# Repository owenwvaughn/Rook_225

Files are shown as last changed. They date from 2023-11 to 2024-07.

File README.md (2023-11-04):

This is a 225x225 build volume printer based on the rook 180 by Rolohaun, 
that uses the BambuLabs P1P hotend in place of the stock hotend.
It's a modification of the work done by woodknight and Kanrog for the rook 180 turned.

It uses an Ender 3 Bed

 [https://github.com/WoodKnight58/Rook-180-Turned](url)

[https://www.printables.com/model/365707-rook-235-225-mod](url)


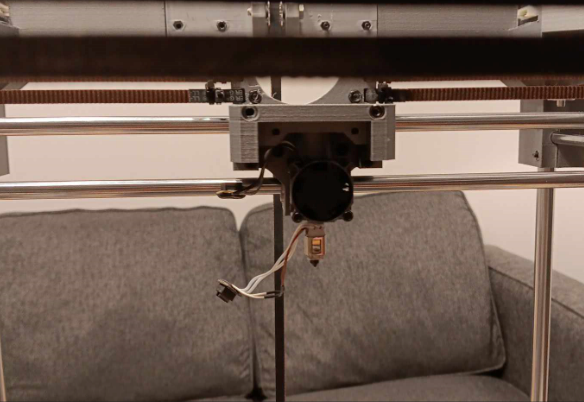
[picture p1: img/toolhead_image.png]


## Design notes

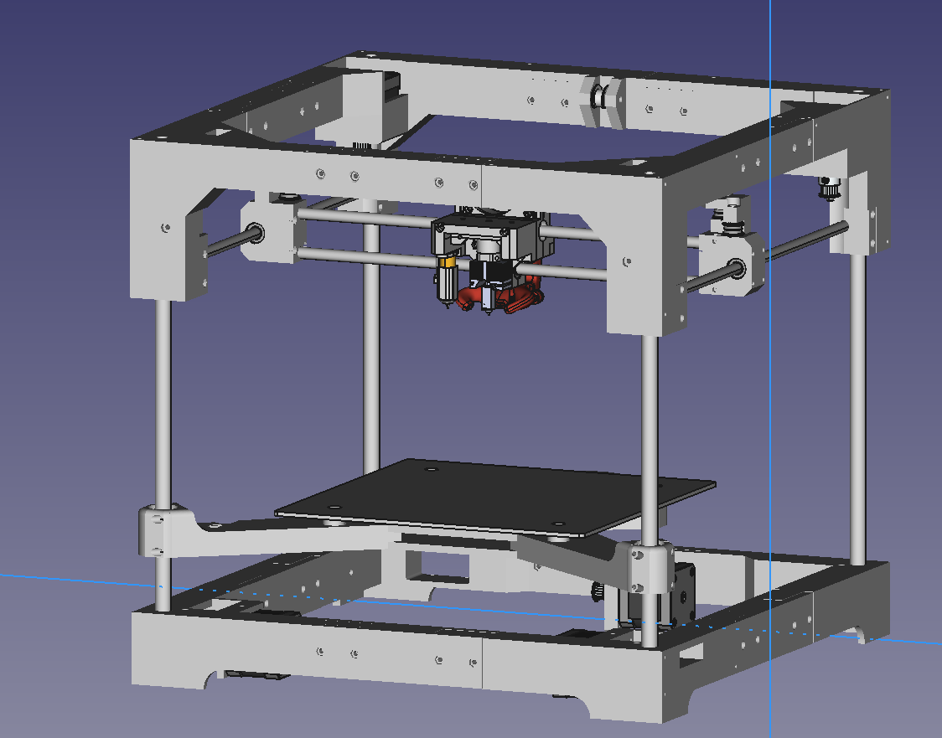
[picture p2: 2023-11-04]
img/frame_image.png

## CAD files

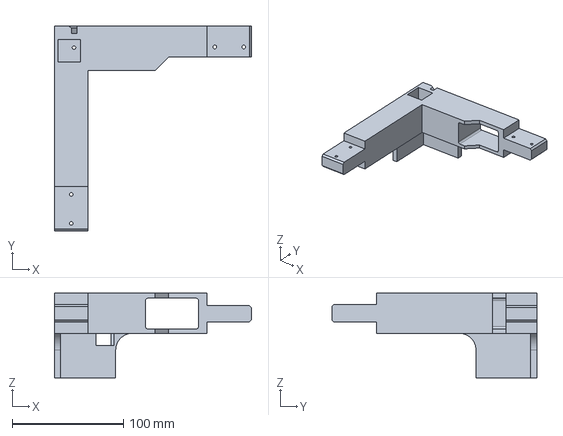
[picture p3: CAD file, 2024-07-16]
printer/cad/FDM/Rear_left_Bottom_Frame.FCStd
177.0 x 184.5 x 76.0 mm

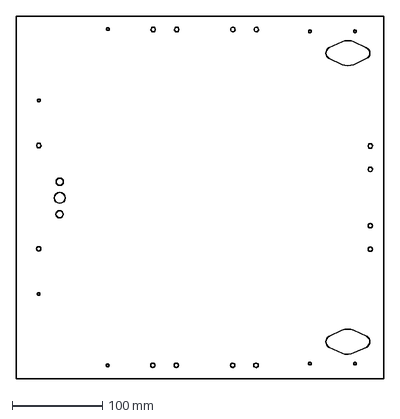
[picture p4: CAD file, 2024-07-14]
printer/cad/MISC/top_panel.dxf
407.3 x 401.7 mm

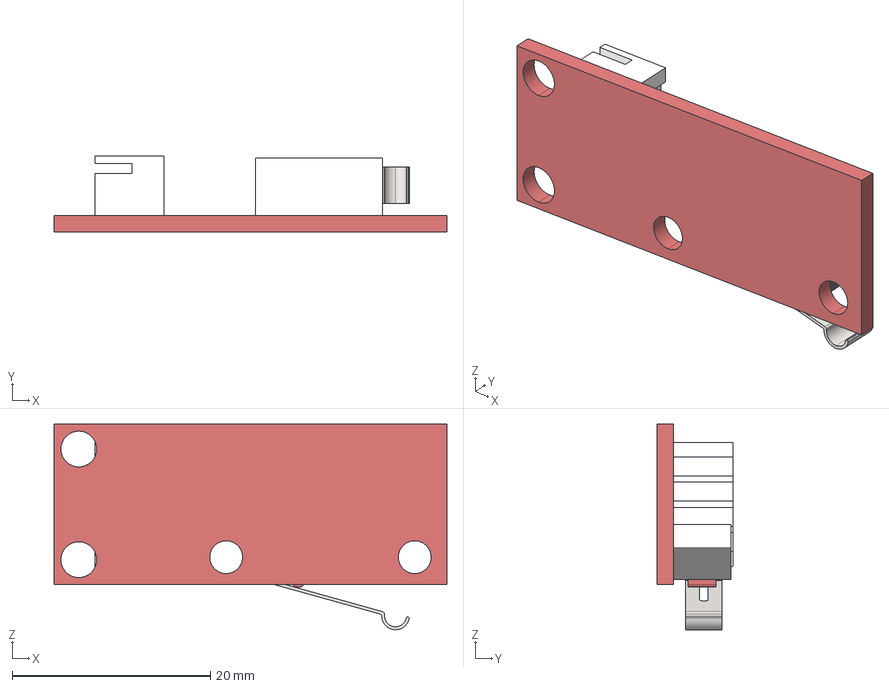
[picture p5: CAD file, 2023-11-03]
printer/cad/PCB/limit-switch.STEP
39.6 x 7.63 x 20.7 mm

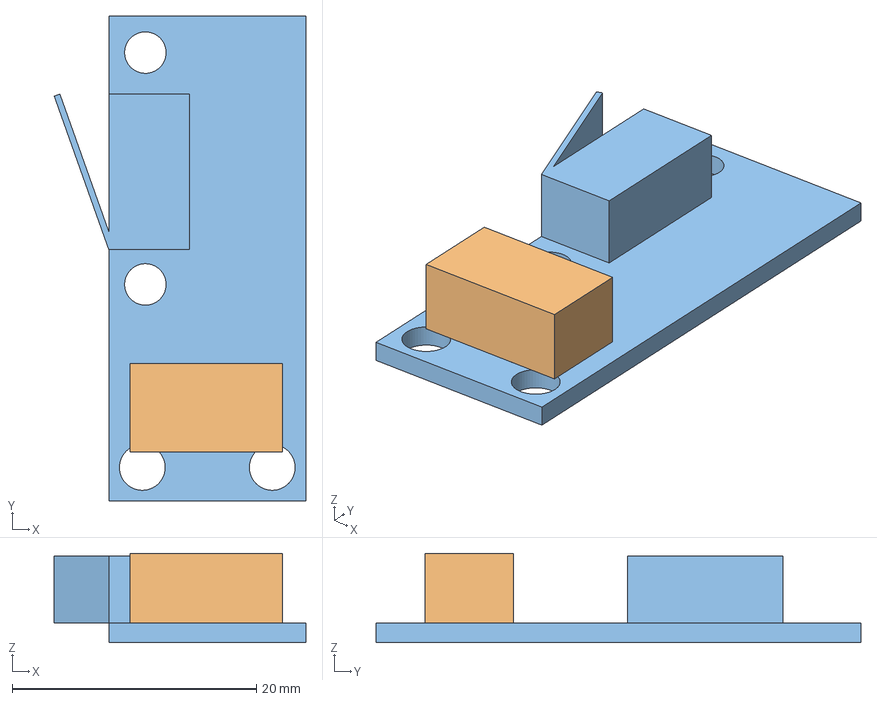
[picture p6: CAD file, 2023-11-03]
printer/pcb/limit-switch/limit-switch.FCStd
20.6 x 39.8 x 7.30 mm

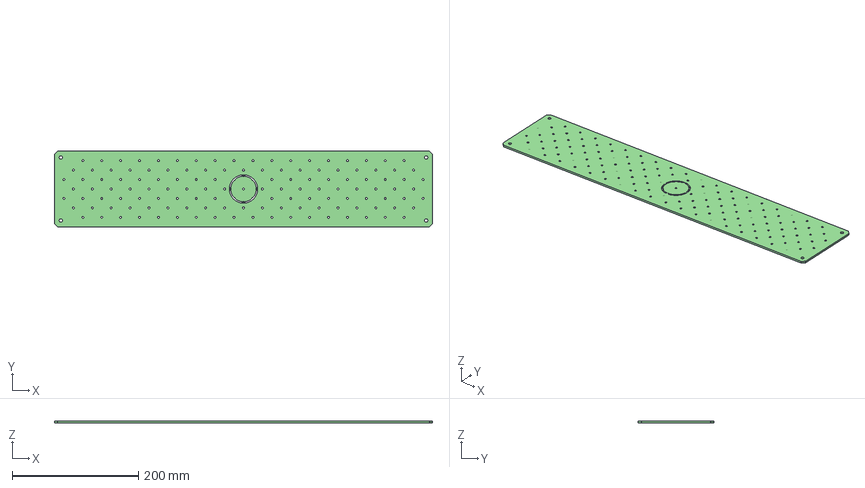
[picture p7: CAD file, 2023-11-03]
printer/pcb/staging-plate/staging-plate.STEP
600.0 x 120.0 x 3.00 mm

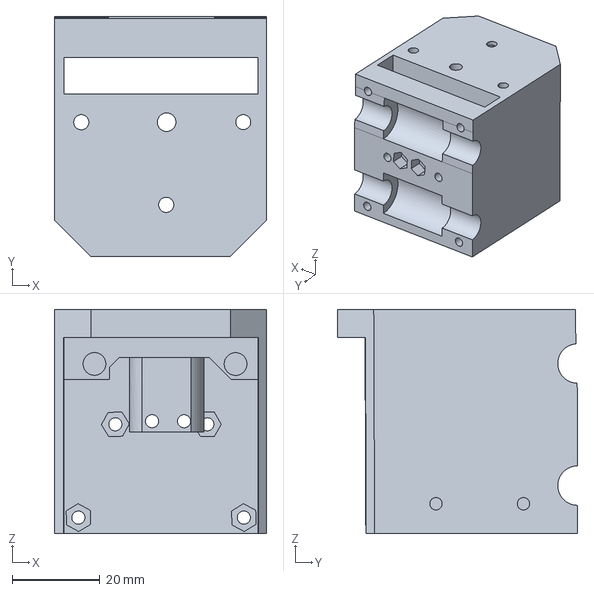
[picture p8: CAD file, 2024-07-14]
printer/cad/FDM/Compact_X_Carriage_Front.FCStd
48.5 x 54.8 x 51.2 mm

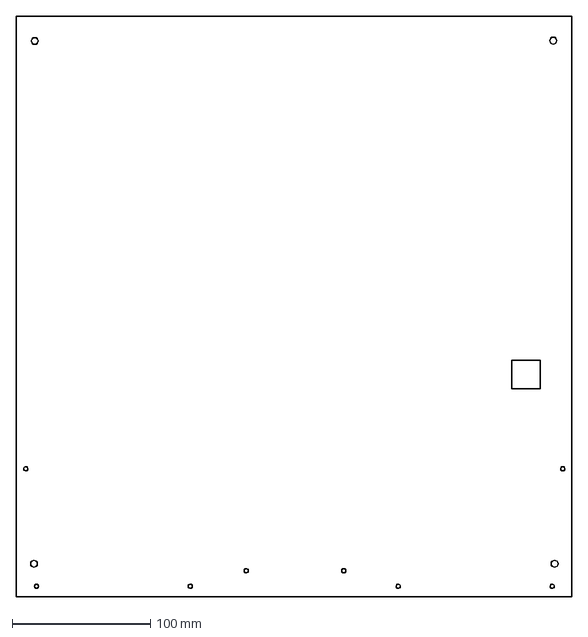
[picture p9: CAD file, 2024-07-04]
printer/cad/MISC/rear_panel.dxf
401.9 x 420.0 mm

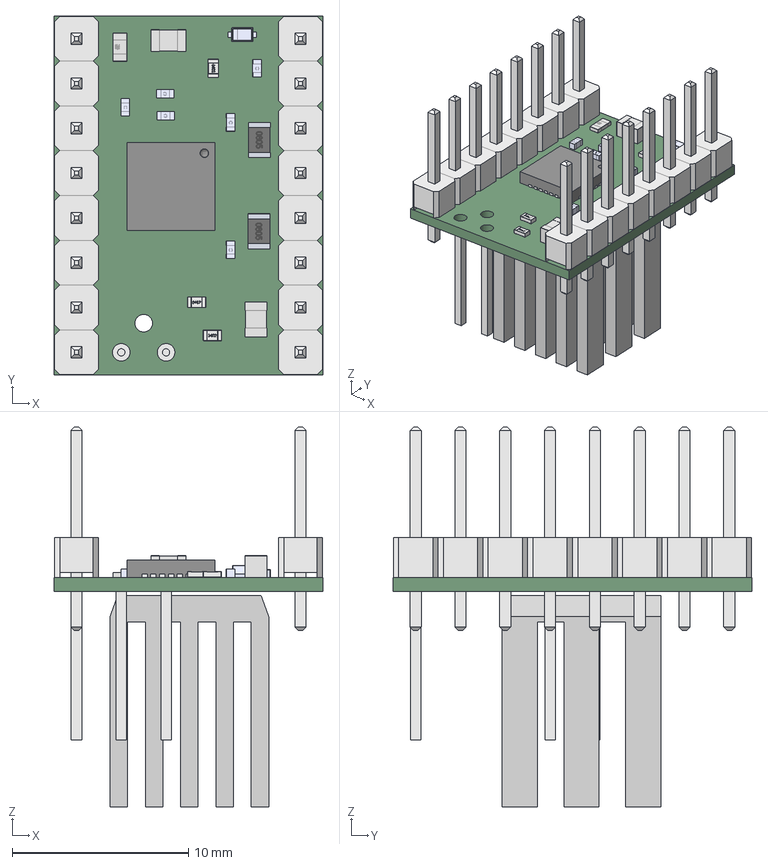
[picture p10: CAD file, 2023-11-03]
printer/cad/PCB/TMC2209-V3_0.FCStd
15.2 x 20.3 x 21.5 mm

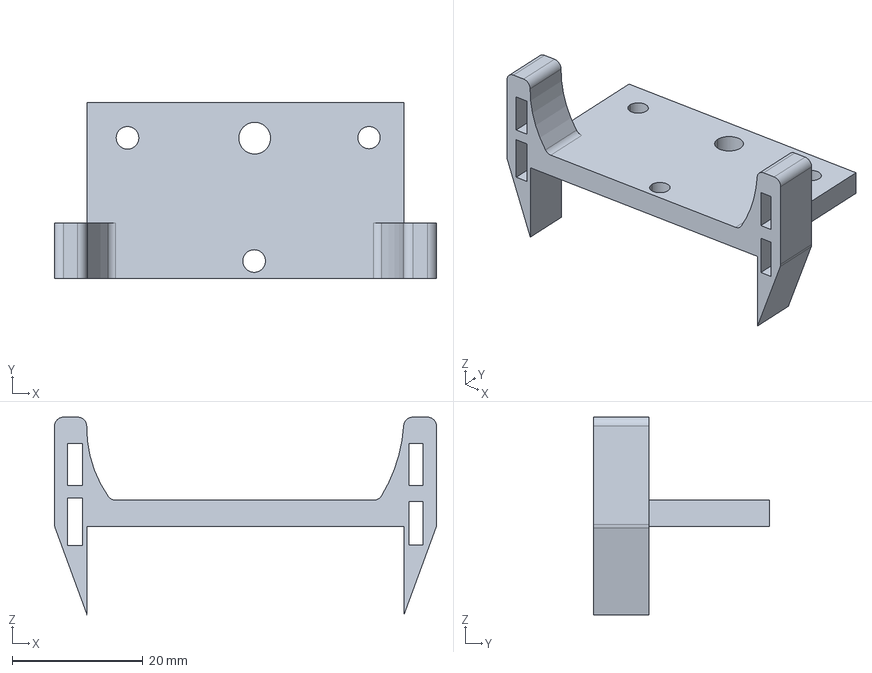
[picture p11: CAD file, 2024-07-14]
printer/cad/FDM/hotend_ears.FCStd
58.5 x 27.0 x 30.3 mm

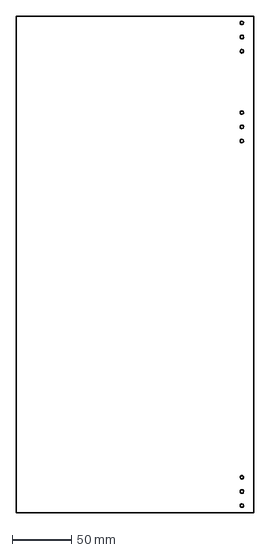
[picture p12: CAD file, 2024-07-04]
printer/cad/MISC/front_panel_left.dxf
200.7 x 419.9 mm

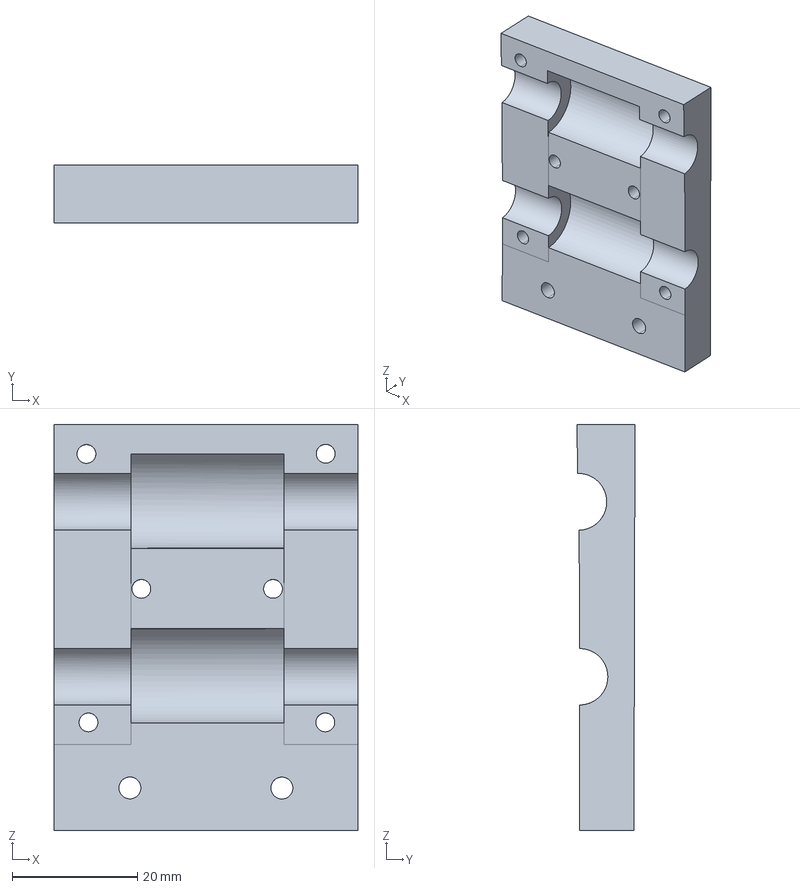
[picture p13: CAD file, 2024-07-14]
printer/cad/FDM/Compact_X_Carriage_Rear.FCStd
48.5 x 9.26 x 64.8 mm

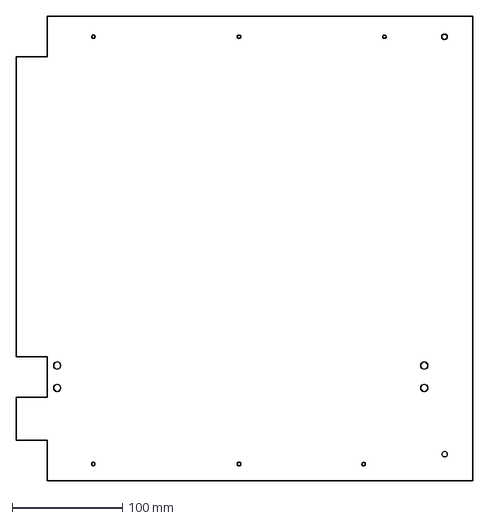
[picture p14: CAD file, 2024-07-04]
printer/cad/MISC/side_panel.dxf
413.8 x 420.4 mm

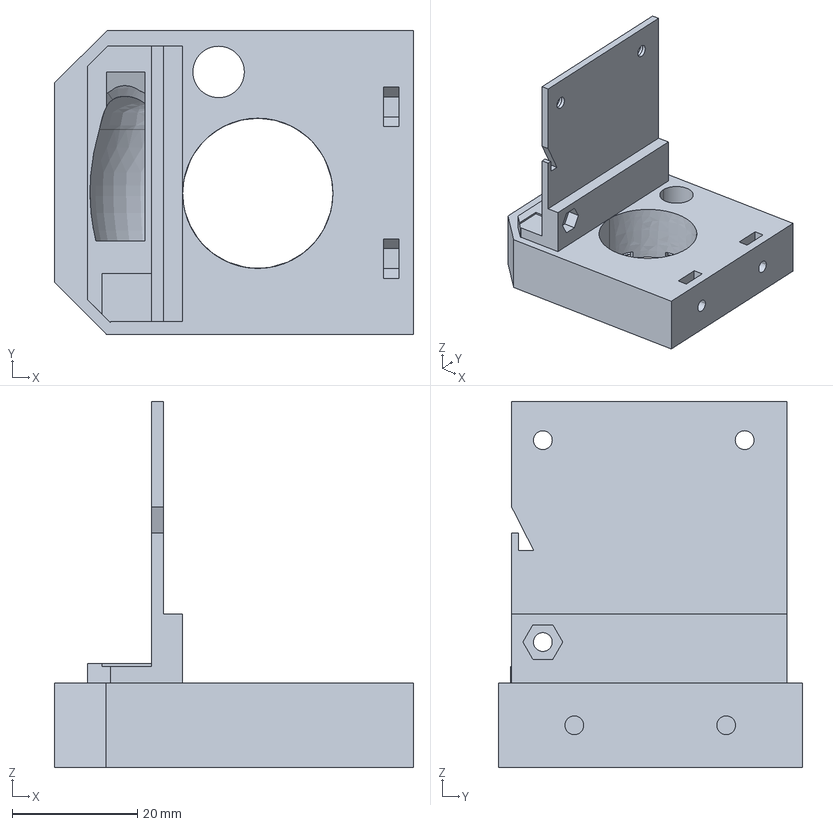
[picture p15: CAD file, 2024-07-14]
printer/cad/FDM/toolhead_toroid.FCStd
57.4 x 48.5 x 58.5 mm

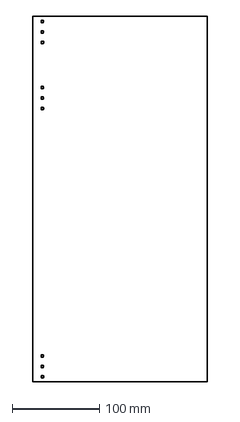
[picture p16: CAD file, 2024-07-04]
printer/cad/MISC/front_panel_right.dxf
200.7 x 419.9 mm

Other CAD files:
printer/cad/FDM/Compact_X_Carriage_Plate.FCStd
printer/cad/FDM/Compact_X_Carriage_Plate-BodyBaseFeature.step
printer/cad/FDM/Bottom_front_right_frame.FCStd
printer/cad/FDM/TOP_Right_Front_Frame.FCStd
printer/cad/FDM/Bed_Standoff.FCStd
printer/cad/FDM/Bed_mount_Center.FCStd
printer/cad/FDM/Bottom_frame_connector.FCStd
printer/cad/FDM/Bottom_front_left_frame.FCStd
printer/cad/FDM/Bottom_front_right_frame_logo.FCStd
printer/cad/FDM/Extrusion_corner.FCStd
printer/cad/FDM/Front_Y_Clamps.FCStd
printer/cad/FDM/Front_frame_tensioner.FCStd
printer/cad/FDM/Hotend_mount_v5.step
printer/cad/FDM/Hotend_mount_v6.step
printer/cad/FDM/Leadscrew_mount_back.FCStd
printer/cad/FDM/Left_Idler_Cartridge.FCStd
printer/cad/FDM/Left_bed_connector.FCStd
printer/cad/FDM/Rear_Lower_brace.FCStd
printer/cad/FDM/Rear_Top_Connector.FCStd
printer/cad/FDM/Rear_right_Bottom_Frame.FCStd
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

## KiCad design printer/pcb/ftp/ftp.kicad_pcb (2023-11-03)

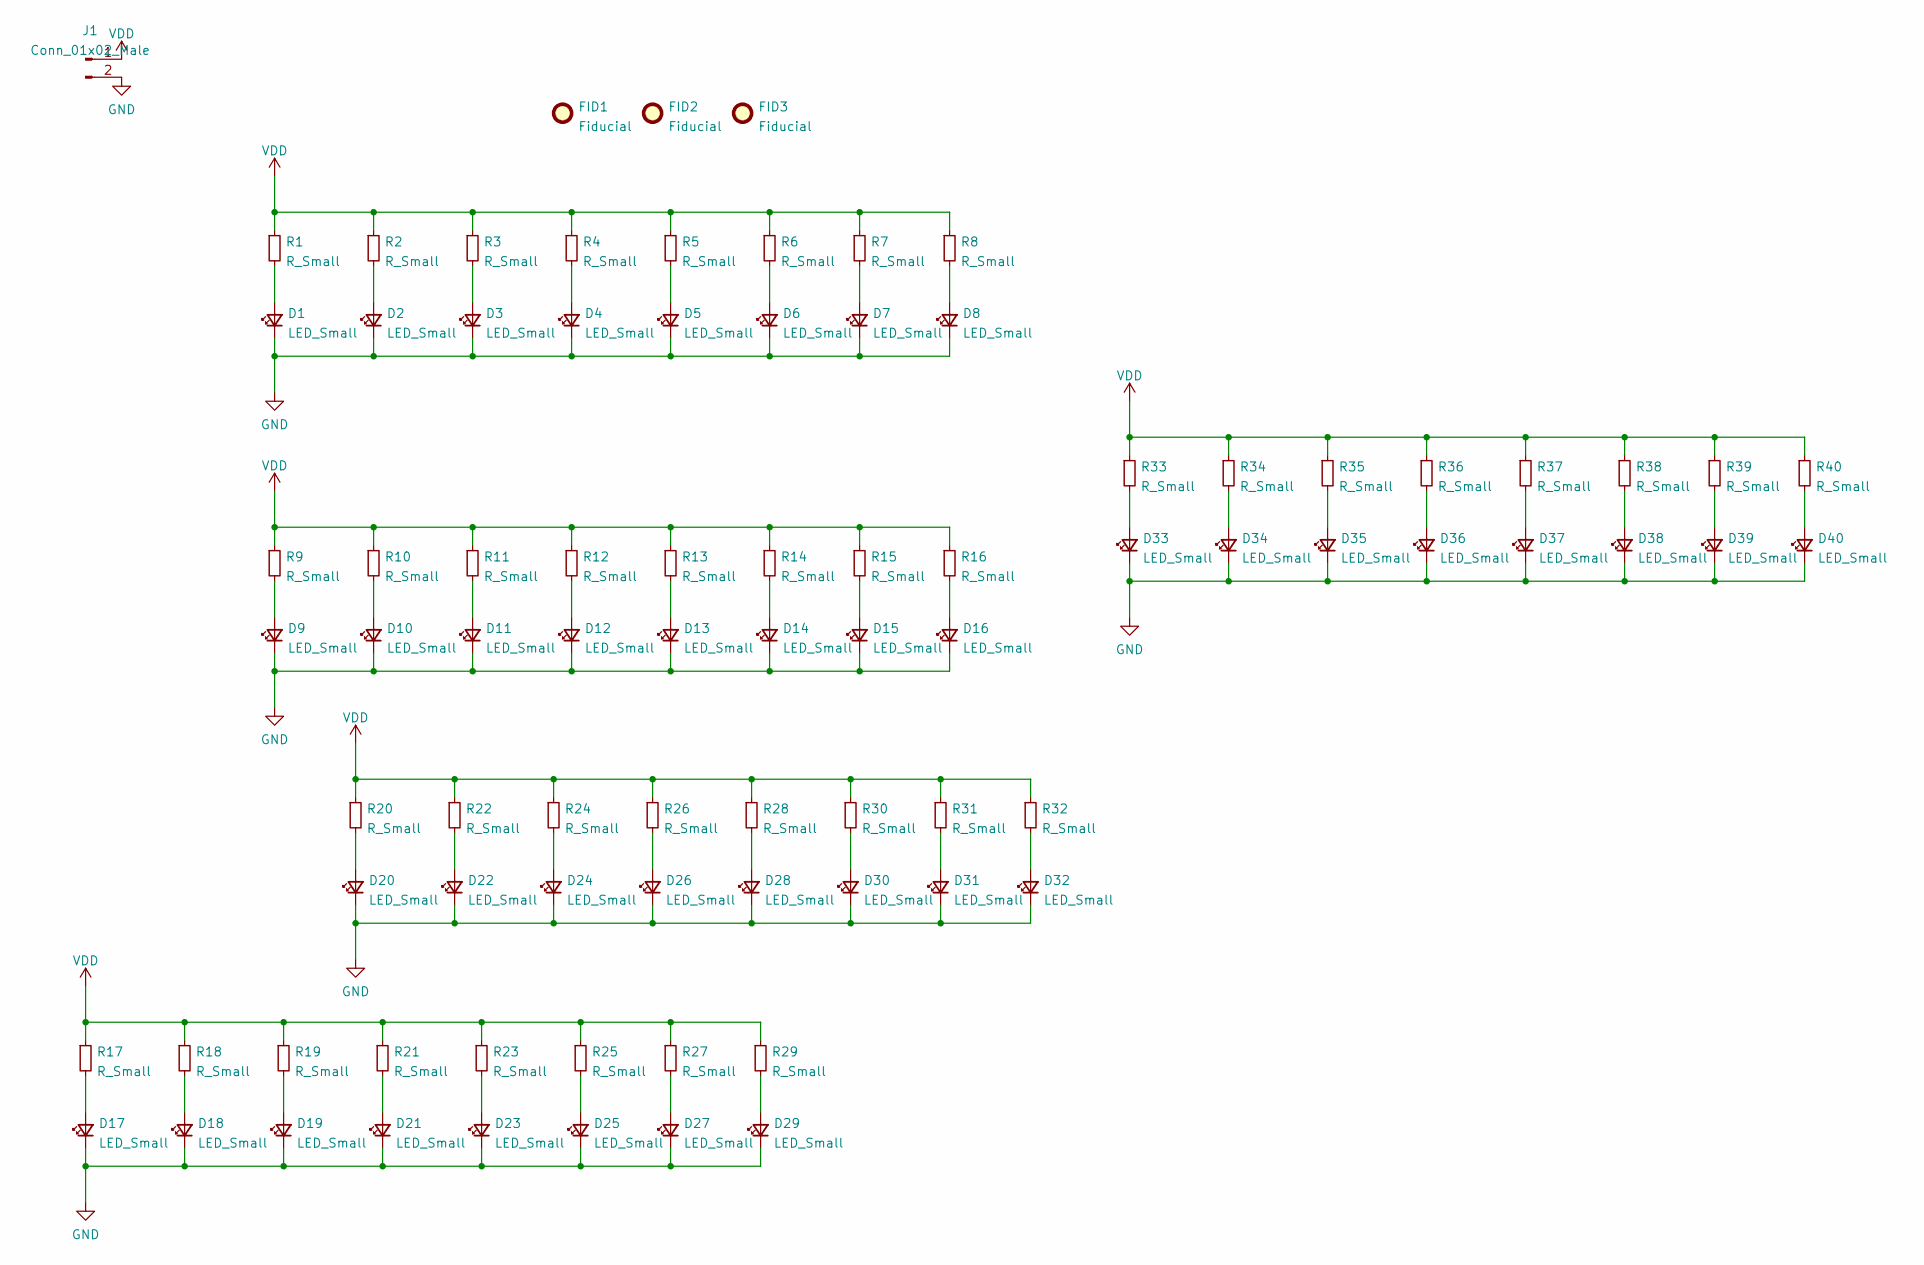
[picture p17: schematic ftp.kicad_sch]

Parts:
D1, D2, D3, D4, D5, D6, D7, D8, D9, D10, D11, D12, D13, D14, D15, D16, D17, D18, D19, D20, D21, D22, D23, D24, D25, D26, D27, D28, D29, D30, D31, D32, D33, D34, D35, D36, D37, D38, D39, D40: LED_Small; LED_0603_1608Metric
FID1, FID2, FID3: Fiducial; Fiducial_1mm_Mask3mm
J1: Conn_01x02_Male; PinHeader_1x02_P2.54mm_Vertical
R1, R2, R3, R4, R5, R6, R7, R8, R9, R10, R11, R12, R13, R14, R15, R16, R17, R18, R19, R20, R21, R22, R23, R24, R25, R26, R27, R28, R29, R30, R31, R32, R33, R34, R35, R36, R37, R38, R39, R40: R_Small; R_0603_1608Metric

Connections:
GND: D1.1 (K), D2.1 (K), D3.1 (K), D4.1 (K), D5.1 (K), D6.1 (K), D7.1 (K), D8.1 (K), D9.1 (K), D10.1 (K), D11.1 (K), D12.1 (K), D13.1 (K), D14.1 (K), D15.1 (K), D16.1 (K), D17.1 (K), D18.1 (K), D19.1 (K), D20.1 (K), D21.1 (K), D22.1 (K), D23.1 (K), D24.1 (K), D25.1 (K), D26.1 (K), D27.1 (K), D28.1 (K), D29.1 (K), D30.1 (K), D31.1 (K), D32.1 (K), D33.1 (K), D34.1 (K), D35.1 (K), D36.1 (K), D37.1 (K), D38.1 (K), D39.1 (K), D40.1 (K), J1.2
unnamed: D1.2 (A), R1.2
unnamed: D2.2 (A), R2.2
unnamed: D3.2 (A), R3.2
unnamed: D4.2 (A), R4.2
unnamed: D5.2 (A), R5.2
unnamed: D6.2 (A), R6.2
unnamed: D7.2 (A), R7.2
unnamed: D8.2 (A), R8.2
unnamed: D9.2 (A), R9.2
unnamed: D10.2 (A), R10.2
unnamed: D11.2 (A), R11.2
unnamed: D12.2 (A), R12.2
unnamed: D13.2 (A), R13.2
unnamed: D14.2 (A), R14.2
unnamed: D15.2 (A), R15.2
unnamed: D16.2 (A), R16.2
unnamed: D17.2 (A), R17.2
unnamed: D18.2 (A), R18.2
unnamed: D19.2 (A), R19.2
unnamed: D20.2 (A), R20.2
unnamed: D21.2 (A), R21.2
unnamed: D22.2 (A), R22.2
unnamed: D23.2 (A), R23.2
unnamed: D24.2 (A), R24.2
unnamed: D25.2 (A), R25.2
unnamed: D26.2 (A), R26.2
unnamed: D27.2 (A), R27.2
unnamed: D28.2 (A), R28.2
unnamed: D29.2 (A), R29.2
unnamed: D30.2 (A), R30.2
unnamed: D31.2 (A), R31.2
unnamed: D32.2 (A), R32.2
unnamed: D33.2 (A), R33.2
unnamed: D34.2 (A), R34.2
unnamed: D35.2 (A), R35.2
unnamed: D36.2 (A), R36.2
unnamed: D37.2 (A), R37.2
unnamed: D38.2 (A), R38.2
unnamed: D39.2 (A), R39.2
unnamed: D40.2 (A), R40.2
VDD: J1.1, R1.1, R2.1, R3.1, R4.1, R5.1, R6.1, R7.1, R8.1, R9.1, R10.1, R11.1, R12.1, R13.1, R14.1, R15.1, R16.1, R17.1, R18.1, R19.1, R20.1, R21.1, R22.1, R23.1, R24.1, R25.1, R26.1, R27.1, R28.1, R29.1, R30.1, R31.1, R32.1, R33.1, R34.1, R35.1, R36.1, R37.1, R38.1, R39.1, R40.1

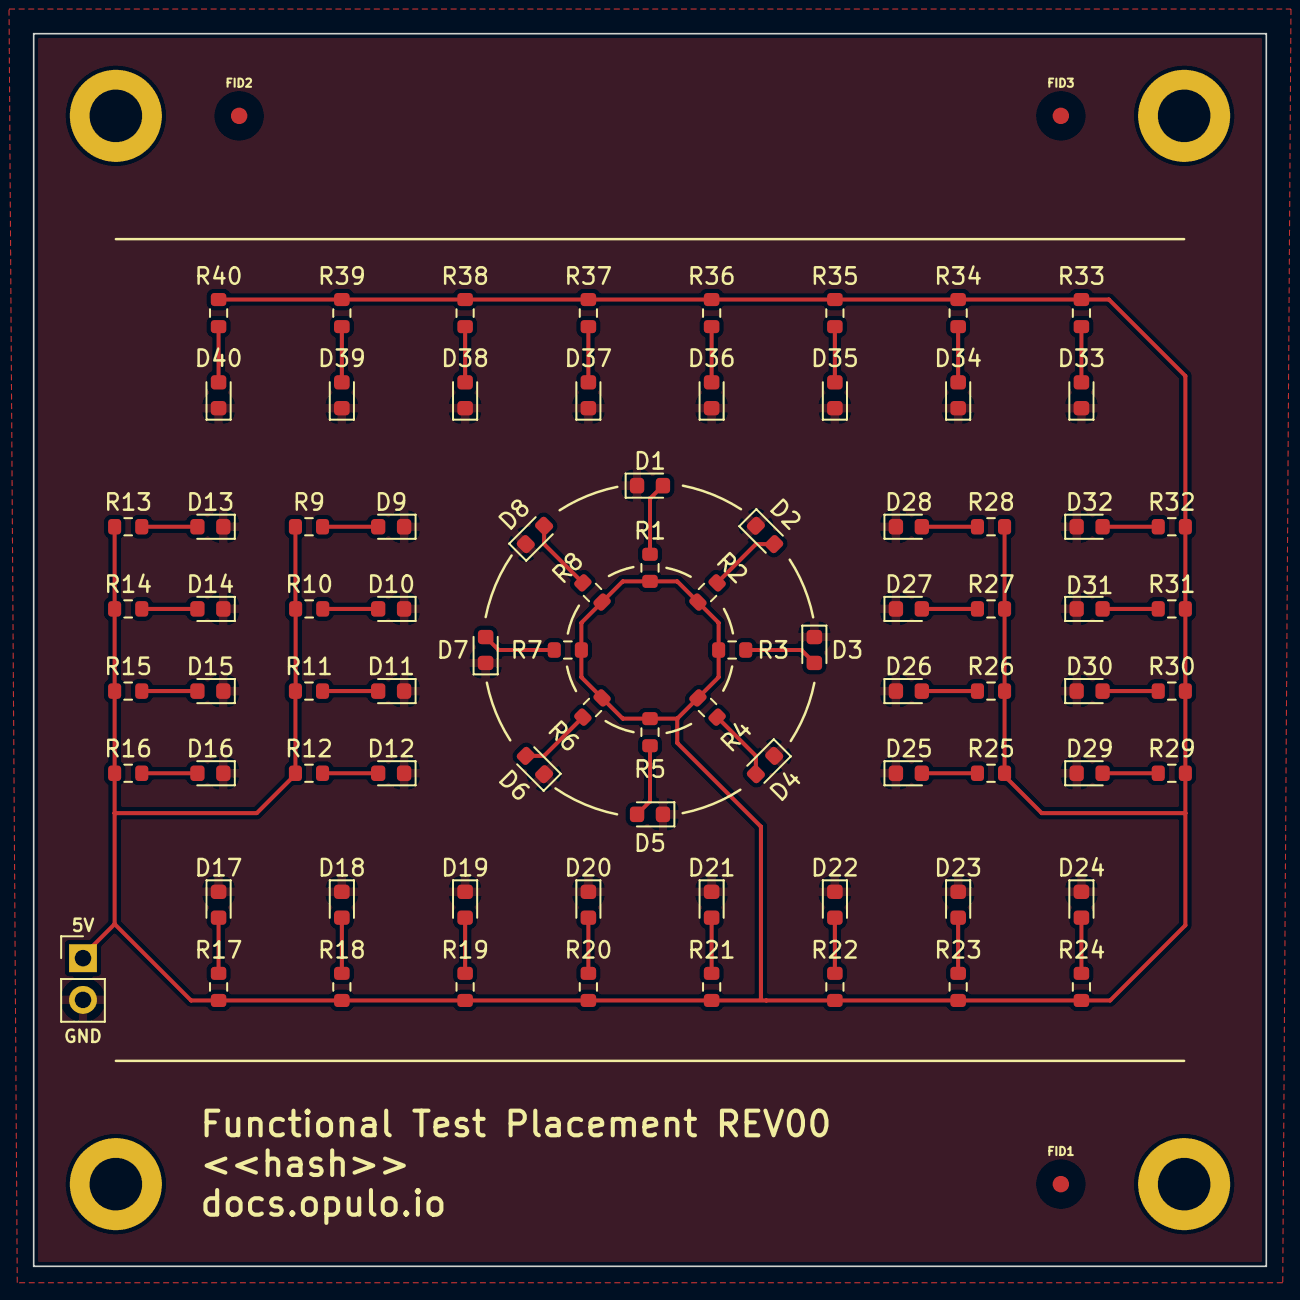
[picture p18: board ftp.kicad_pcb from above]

Board: 2 copper layers, 75.0 x 75.0 mm, 84 parts (0 on the bottom side), 42 nets.

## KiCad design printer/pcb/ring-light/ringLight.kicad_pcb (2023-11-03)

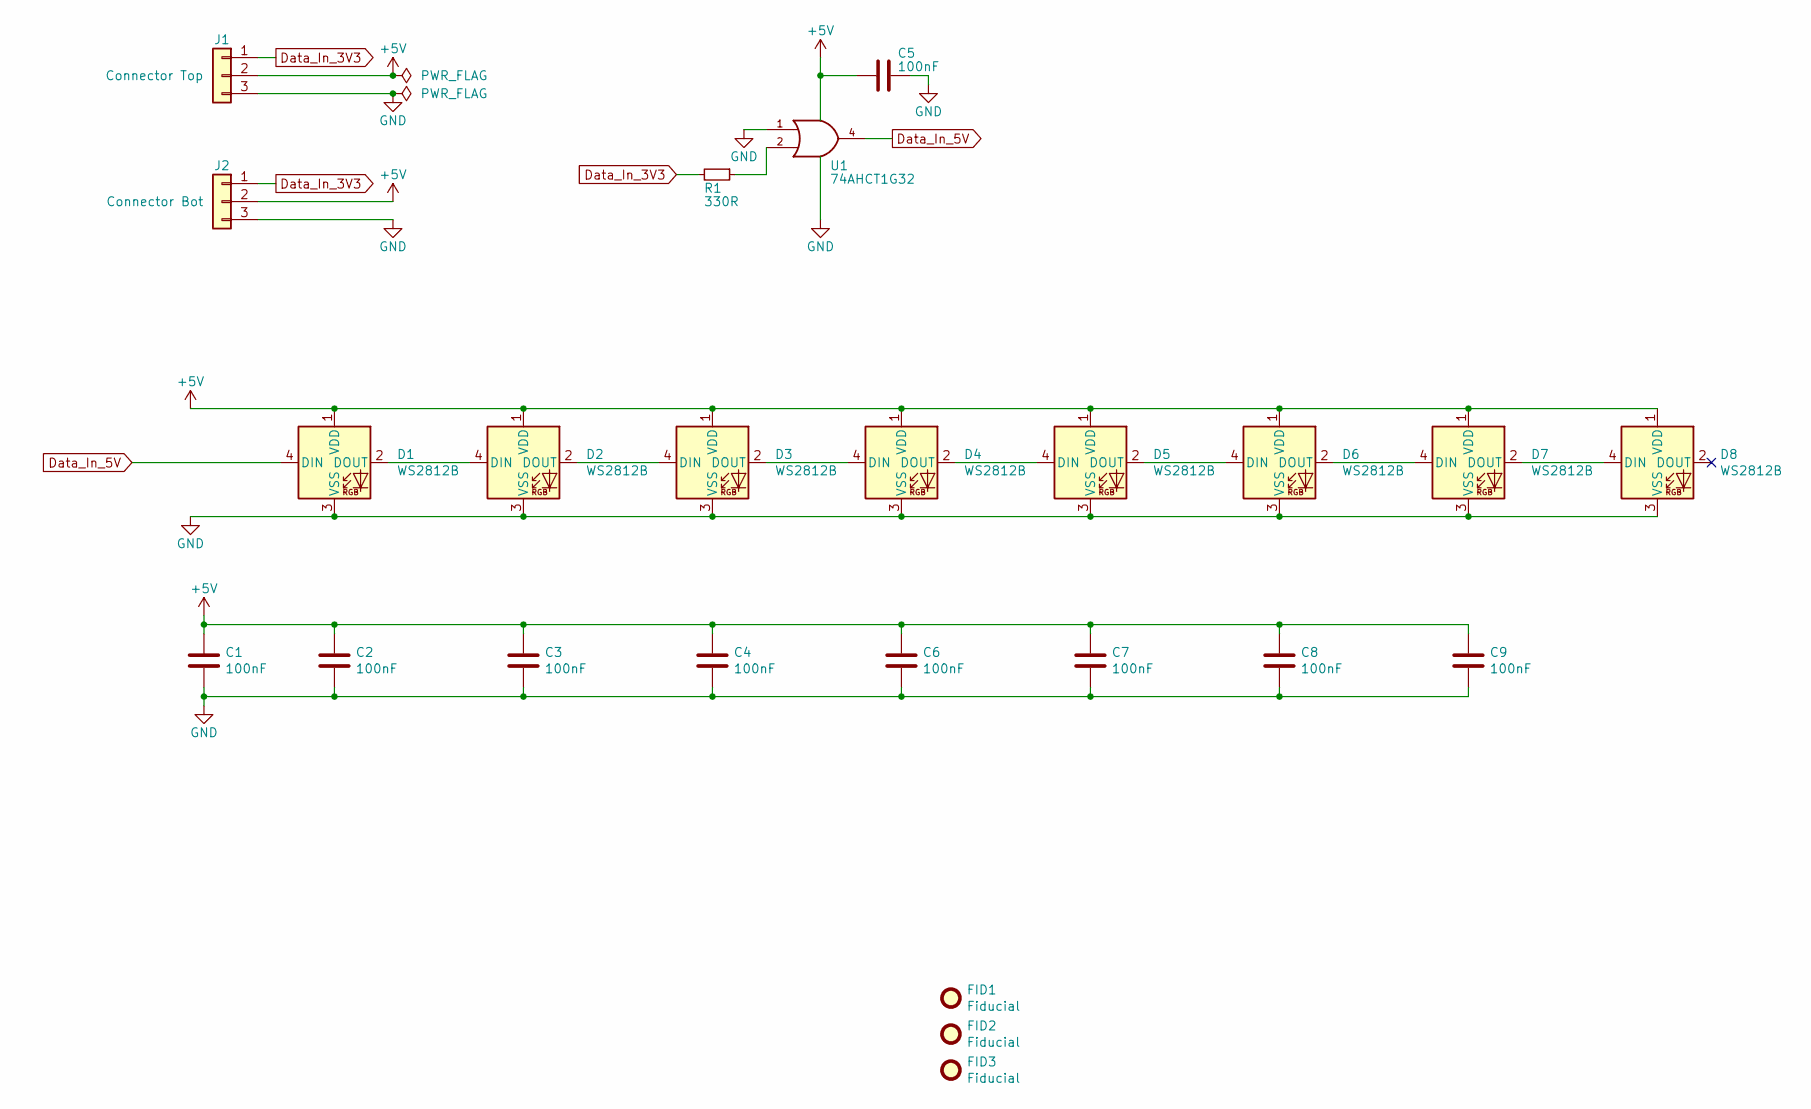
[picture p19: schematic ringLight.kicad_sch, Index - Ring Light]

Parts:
C1, C2, C3, C4, C5, C6, C7, C8, C9: 100nF; C_0805_2012Metric; Part # CC0805KRX7R9BB104; JLCPCB C49678
D1, D2, D3, D4, D5, D6, D7, D8: WS2812B; LED_WS2812B_PLCC4_5.0x5.0mm_P3.2mm; Part # WS2812B; JLCPCB C114586
FID1, FID2, FID3: Fiducial; Fiducial_1mm_Mask2mm
J1: Connector Top; JST_XH_B3B-XH-A_1x03_P2.50mm_Vertical; Part # B3B-XH-A(LF)(SN); JLCPCB C144394
J2: Connector Bot; JST_XH_S3B-XH-A-1_1x03_P2.50mm_Horizontal; Part # S3B-XH-A-1(LF)(SN); JLCPCB C163036
R1: 330R; R_0805_2012Metric; Part # 0805W8F3300T5E; JLCPCB C17630
U1: 74AHCT1G32; SOT-353_SC-70-5; JLCPCB C43450

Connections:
+5V: C1.1, C2.1, C3.1, C4.1, C5.1, C6.1, C7.1, C8.1, C9.1, D1.1 (VDD), D2.1 (VDD), D3.1 (VDD), D4.1 (VDD), D5.1 (VDD), D6.1 (VDD), D7.1 (VDD), D8.1 (VDD), J1.2, J2.2, U1.5 (VCC); also elsewhere on the board
Data_In_3V3: J1.1, J2.1, R1.2
Data_In_5V: D1.4 (DIN), U1.4
GND: C1.2, C2.2, C3.2, C4.2, C5.2, C6.2, C7.2, C8.2, C9.2, D1.3 (VSS), D2.3 (VSS), D3.3 (VSS), D4.3 (VSS), D5.3 (VSS), D6.3 (VSS), D7.3 (VSS), D8.3 (VSS), J1.3, J2.3, U1.1, U1.3 (GND); also elsewhere on the board
unnamed: D1.2 (DOUT), D2.4 (DIN)
unnamed: D2.2 (DOUT), D3.4 (DIN)
unnamed: D3.2 (DOUT), D4.4 (DIN)
unnamed: D4.2 (DOUT), D5.4 (DIN)
unnamed: D5.2 (DOUT), D6.4 (DIN)
unnamed: D6.2 (DOUT), D7.4 (DIN)
unnamed: D7.2 (DOUT), D8.4 (DIN)
unnamed: R1.1, U1.2

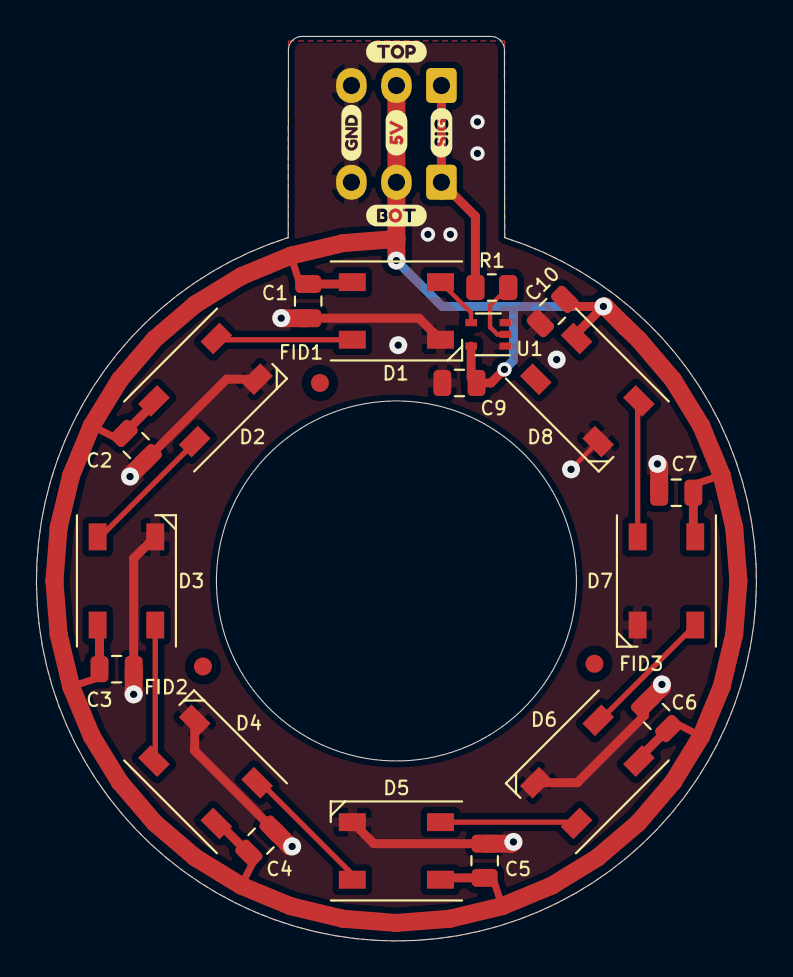
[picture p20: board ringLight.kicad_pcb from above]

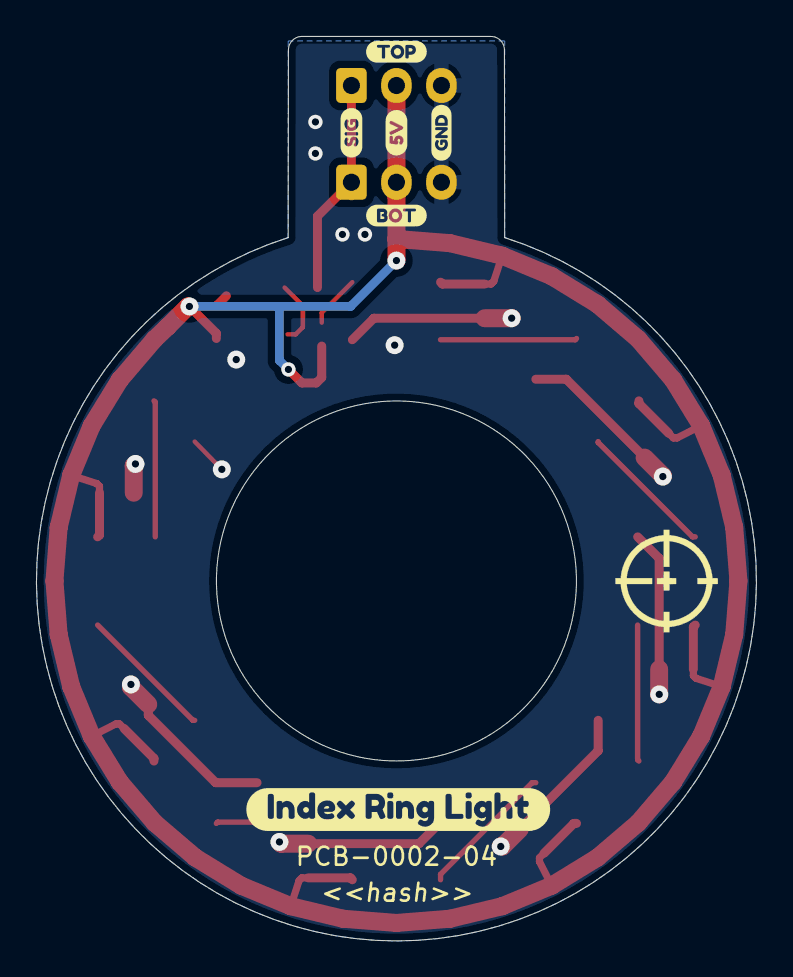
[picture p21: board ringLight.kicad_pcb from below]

Board: 2 copper layers, 40.0 x 50.2 mm, 36 parts (8 on the bottom side), 12 nets.

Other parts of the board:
C10: 100nF; C_0805_2012Metric
LOGO: LOGO; logo
kibuzzard-61F2BC8D, kibuzzard-61F2BC8D#2: G***; kibuzzard-61F2BC8D
kibuzzard-61F2BC9E, kibuzzard-61F2BC9E#2: G***; kibuzzard-61F2BC9E
kibuzzard-61F2BC96, kibuzzard-61F2BC96#2: G***; kibuzzard-61F2BC96
kibuzzard-61F2BEFE: G***; kibuzzard-61F2BEFE
kibuzzard-61F2BF3C: G***; kibuzzard-61F2BF3C
kibuzzard-61F2BF4A: G***; kibuzzard-61F2BF4A
kibuzzard-61F2BF10: G***; kibuzzard-61F2BF10
svg2mod: n/a; label

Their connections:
+5V: C10.1; also elsewhere on the board
GND: C10.2; also elsewhere on the board

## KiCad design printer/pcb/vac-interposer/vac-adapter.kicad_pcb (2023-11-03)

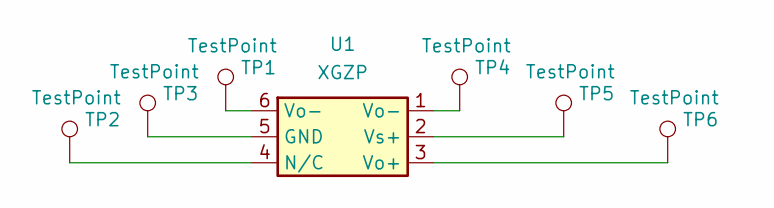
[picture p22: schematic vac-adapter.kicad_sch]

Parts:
TP1, TP2, TP3, TP4, TP5, TP6: TestPoint; TestPoint_THTPad_1.0x1.0mm_Drill0.5mm
U1: XGZP; SO-6_7x7mm_P2.54mm

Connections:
unnamed: TP1.1, U1.6 (Vo-)
unnamed: TP2.1, U1.4 (N/C)
unnamed: TP3.1, U1.5 (GND)
unnamed: TP4.1, U1.1 (Vo-)
unnamed: TP5.1, U1.2 (Vs+)
unnamed: TP6.1, U1.3 (Vo+)

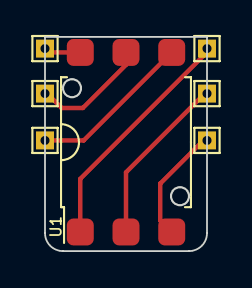
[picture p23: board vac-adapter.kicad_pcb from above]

Board: 2 copper layers, 9.0 x 11.9 mm, 7 parts (0 on the bottom side), 6 nets.

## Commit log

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2023-11-12 Added new version of the hotend
    Added new version of the hotend mount, and gave it a heat set insert set screw so that the hotend can't wiggle.
    [P1P-hotend.FCStd, y_clamp.step]
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2023-11-29 Making things cheaper
    The back frame used linear rods when they weren't necessary. Replacing them with aluminum extrusion to cut down on cost.
    [TOP_Left_Rear_Frame_extrusion.FCStd, TOP_Right_Rear_Frame_extrusion.FCStd]
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2023-12-01 Added Chamfers to frame pieces
    Added Chambers to frame pieces so that when they're printed, they're more likely to fit nicely together.
    [Rear_left_Bottom_Frame.FCStd, Rear_right_Bottom_Frame.FCStd, TOP_Left_Front_Frame.FCStd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]
2023-12-10 Adjusted tolerances for frame pieces
    [Rear_Lower_brace.FCStd, Rear_Top_Connector.FCStd]
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2024-01-24 Re-modeled the hotend mount.
    The new hotend mount is more similar to p1p's stock method of mounting.
    [Hotend_mount_v6.step]
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2024-04-18 Belt tensioning changes.
    The A and B belts are now able to be tightened independently of one another because of the M5 nut captive nut that can be used to push the motors back.
    [TOP_Left_Rear_Frame_extrusion.FCStd, TOP_Right_Rear_Frame_extrusion.FCStd]
2024-04-24 Adjusted Tolerances.
    [Bottom_frame_connector.FCStd, Rear_Lower_brace.FCStd, Rear_left_Bottom_Frame.FCStd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]
2024-04-26 Added holes for t nut mounting / adjusted tolerance
    [Rear_left_Bottom_Frame.FCStd, Rear_right_Bottom_Frame.FCStd, TOP_Left_Rear_Frame_extrusion.FCStd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]
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2024-05-04 Adjusted Height of feet
    Needed to lengthen the feet of the printer so that they could clear the z motors at the bottom.
    [Bottom_front_left_frame.FCStd, Bottom_front_right_frame.FCStd, Rear_left_Bottom_Frame.FCStd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]
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2024-05-05 Added a leadscrew mount in the back.
    Lengthened legs and added leadscrew mount in the back.
    [Bottom_front_left_frame.FCStd, Bottom_front_right_frame.FCStd, Leadscrew_mount_back.FCStd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]
2024-05-06 Added places for mounting of lead screws
    Also added places for linear rods to be placed.
    [Leadscrew_mount_back.FCStd]
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2024-05-07 Adjusted Rear leadscrew mount
    Adjusted the rear leadscrew mount at the top to allow for more y Axis travel of the toolhead.
    [Rear_upper_brace.FCStd]
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2024-05-09 Finished rear_back_leadscrew_mount
    Aligned the rear leadscrew stuff to the middle so that everything was nice and evenly aligned.
    [Leadscrew_mount_back.FCStd]
2024-05-10 Timing belt_added
    Z_axis timing belts have been added.
    Had to make a compromise of using two different 750mm belts because there isn't an easy way to get closed loop belts of sufficient size to go around all 3 pulleys.
    [Rear_upper_brace.FCStd, Rear_upper_central_brace.FCStd]
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2024-05-10 Adjusted tolerances
    [Bottom_frame_connector.FCStd]
2024-05-14 Changed front top pieces to not need support
    Front pieces don't need support, and now they have a space for the KFL08 bearings.
    [Left_Idler_Cartridge.FCStd, Right_Idler_Cartridge.FCStd, TOP_Left_Front_Frame.FCStd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]
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2024-05-16 Added new method of z belt tensioning.
    Dropped the two belt design, and used just one belt that's 1142mm
    [Front_frame_tensioner.FCStd, Tensioner_extension.FCStd, sliding_body.FCStd]
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2024-05-20 adjusted tolerances on sliding body.
    Adjusted tolerances on sliding body so that it could be more easily pulled back by the screw, thus allowing belt tensioning to be done more easily on the Z axis.
    [sliding_body.FCStd]
2024-05-20 bed center_mount
    Added the centerpiece of the bed mount, and some standoffs
    [Bed_Standoff.FCStd, Bed_mount_Center.FCStd]
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2024-05-22 Fixing sliding body hole size again for a proper friction fit
    [sliding_body.FCStd]
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2024-05-24 Finished back connector
    Also made it possible to actually assemble the z axis.
    [Bed_mount_Center.FCStd, Left_bed_connector.FCStd, Tensioner_extension.FCStd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]
2024-05-26 Redesigned Z Tensioner
    [Tensioner_extension.FCStd, idler_holder.FCStd]
2024-05-26 Adjujsted all back frame parts to go 10mm out
    All back frame parts extend 10mm backward now, to allow for the printer to properly be enclosed.
    Additionally, redid all bed couplers to be much much easier to assemble.
    Re-did the size of the idler sliding body for the z axis so that it is able to properly fit a belt into it along with the bolt and the idler.
    [Leadscrew_mount_back.FCStd, Left_bed_connector.FCStd, Rear_left_Bottom_Frame.FCStd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]
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2024-05-28 Made back top corners supportless.
    Modified the back top corners so that they no longer need to be printed with supports. Changed the couplers to accomodate.
    [TOP_Left_Rear_Frame_extrusion.FCStd, TOP_Right_Rear_Frame_extrusion.FCStd, back_left_y_coupler.FCStd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]
2024-05-29 Added optional logo piece.
    Added optional logo piece for the bottom front right corner.
    [Bottom_front_right_frame_logo.FCStd]
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2024-05-31 Adjusted legs so bottom panel was more simple.
    Also added places for bottom panel to mount onto the bottom of the frame.
    [Bottom_front_left_frame.FCStd, Bottom_front_right_frame.FCStd, Rear_left_Bottom_Frame.FCStd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]
2024-05-31 Numerous changes.
    Added cable routing channels on the back corner pieces, that are then clamped down/hidden by the back panel.
    Adjusted the A and B motor mounts to be able to slide back and forth so that they can be independently tensioned correctly.
    Added the beginnings of hinges to the front of the printer on the top side.
    [Rear_left_Bottom_Frame.FCStd, Rear_right_Bottom_Frame.FCStd, TOP_Left_Front_Frame.FCStd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]
2024-06-02 Added Front door
    Added front door and hinges. The previous print in place version of the design wouldn't have allowed me to place the hinges on the side and then have a 90 degree turn.
    [Bottom_front_left_frame.FCStd, Bottom_front_right_frame.FCStd, TOP_Left_Front_Frame.FCStd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]
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2024-06-03 So much stuff.
    Made panel designs for the enclosure.
    Moved away from having the weird stub, so that I could later put a magnet on the door.
    Changed the design of the right y carriage to make it possible to get the full travel over the bed.
    Made changes to the back center pieces on the top and bottom to allow for cable routing.
    [Bottom_front_right_frame.FCStd, Leadscrew_mount_back.FCStd, Rear_right_Bottom_Frame.FCStd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]
2024-06-04 Fixed dumb y axis mistakes
    [Y_carriage_left.FCStd, Y_carriage_right.FCStd, y_clamp.step]
2024-06-05 Adjusted tolerances for y axis 350mm rods.
    [TOP_Left_Front_Frame.FCStd, TOP_Left_Rear_Frame_extrusion.FCStd, TOP_Right_Front_Frame.FCStd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]
2024-06-06 Wire path routing changes.
    Took advice from Lucian, decided not to have the cables come out the back and just pack everything into much deeper grooves in the sides of the frame.
    [Rear_left_Bottom_Frame.FCStd, Rear_right_Bottom_Frame.FCStd, Rear_upper_central_brace.FCStd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]
2024-06-07 Remodeled y carriage left.
    For some reason it did weird things when thrown into slicers, so I just remodeled it, and the problem went away.
    [Y_carriage_left.FCStd, Y_carriage_right.FCStd, y_clamp.step]
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2024-06-28 rotated the sketches for the panels
    Also added the svg for the 4 panels that aren't the top and bottom.
    [laser_cut_panels.FCStd]
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2024-06-28 Adjusted front panel, added handles
    Adjusted front panel, added panels, added relief in front panel left bottom to allow screws to poke through slighly into the printed part for extra tolerance.
    [Bottom_front_left_frame.FCStd, handle.FCStd, handle_cap.FCStd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]
2024-07-04 Door,frame,and panel changes.
    Added top panel.
    Switched from 1 front door to 2 to doors to prevent sagging. Added mounting points on the other side of the frame at the front so that another door could be added.
    [Bed_mount_Center.FCStd, Bottom_front_left_frame.FCStd, Bottom_front_right_frame.FCStd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]
2024-07-06 Changed the plate on the front
    Adjusted tolerance to the front plate of the toolhead, as it was interfering with the fan.
    [Compact_X_Carriage_Plate-BodyBaseFeature.step, Compact_X_Carriage_Plate.FCStd]
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
